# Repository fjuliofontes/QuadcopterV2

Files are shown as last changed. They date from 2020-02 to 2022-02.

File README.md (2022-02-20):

# Quadcopter V2
## This repository contains a work in progress of the second version of my previous quadcopter project.
## This version will support all modes of control.

### Main controller board hardware:
  - 1 x [ESP-01 for Wifi support](https://www.aliexpress.com/item/33018645469.html)
  - 1 x [HC-SR04 for landing support](https://www.aliexpress.com/item/32981718332.html)
  - 1 x [HC-05 for Bluetooth support](https://www.aliexpress.com/item/32953559442.html)
  - 2 x [HC-12 for RF communication](https://www.aliexpress.com/item/32971735328.html)
  - 1 x [MPU-6050 gyro/accelerometer for auto-level feature](https://www.aliexpress.com/item/32346328217.html)
  - 1 x [MS5611 Barometer for altitude hold function](https://www.aliexpress.com/item/4000436844936.html)
  - 1 x [SIM800L V2 for GSM & TCP communication](https://www.aliexpress.com/item/32467842817.html)
  - 1 x [U-blox M8 Engine GPS for heading lock and GPS hold function](https://www.dx.com/p/72-channel-u-blox-m8-engine-gps-module-for-fpv-multicopter-black-2069966.html)
  - 1 x [Texas-EK-TM4C123GXL for running the main software](http://www.ti.com/tool/EK-TM4C123GXL)
  
 ### Quadcopter housing hardware:
  - 1 x [450 size frame with integrated power distribution board](https://www.aliexpress.com/item/4000129400366.html)
  - 4 x [1000kV motor / 10x4.5 props / ESC combo](https://www.aliexpress.com/item/2035093137.html)
  - 1 x [3S / 2200mAh / 30C lipo](https://www.dx.com/p/11-1v-2200mah-30c-li-polymer-battery-pack-for-450-helicopter-dji-phantom-1-450-quadcopter-2048977.html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)
  - 1 x [Battery XT60 connector](https://www.aliexpress.com/item/33061763696.html)
  - 1 x [2S/3S lipo battery charger](https://www.aliexpress.com/item/4000106254839.html)
  
  #### [Version 1.0](https://github.com/fjuliofontes/Quadcopter)
  
  ##### TODO:
  - [x] Order the necessary hardware.
  - [x] Test and develop code for ordered hardware.
  - [x] Design a schematic and a board for the hardware.
  - [x] Develop a controller algorithm for the quadcopter.
  - [x] Update the android remote controller application.
  - [x] Testing all together. 
  
  ##### Media:
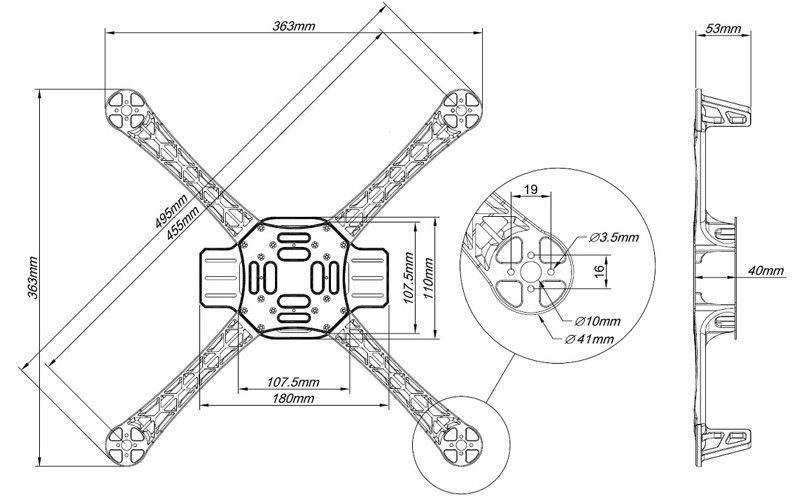
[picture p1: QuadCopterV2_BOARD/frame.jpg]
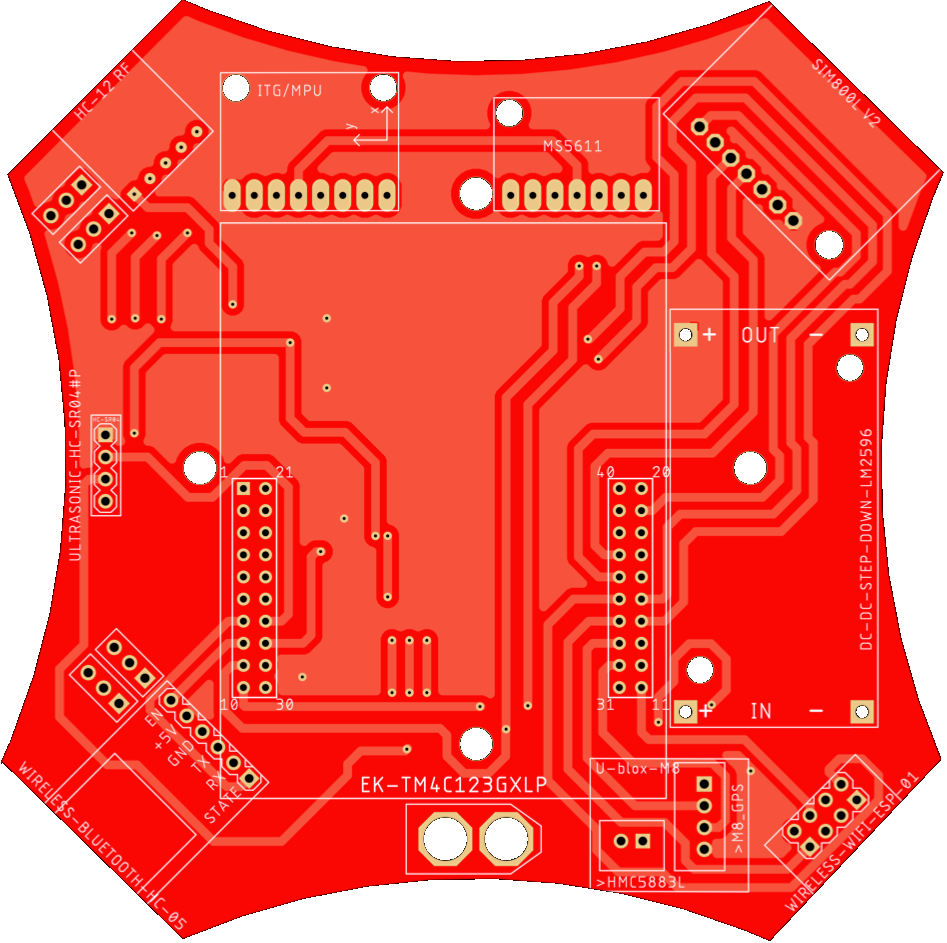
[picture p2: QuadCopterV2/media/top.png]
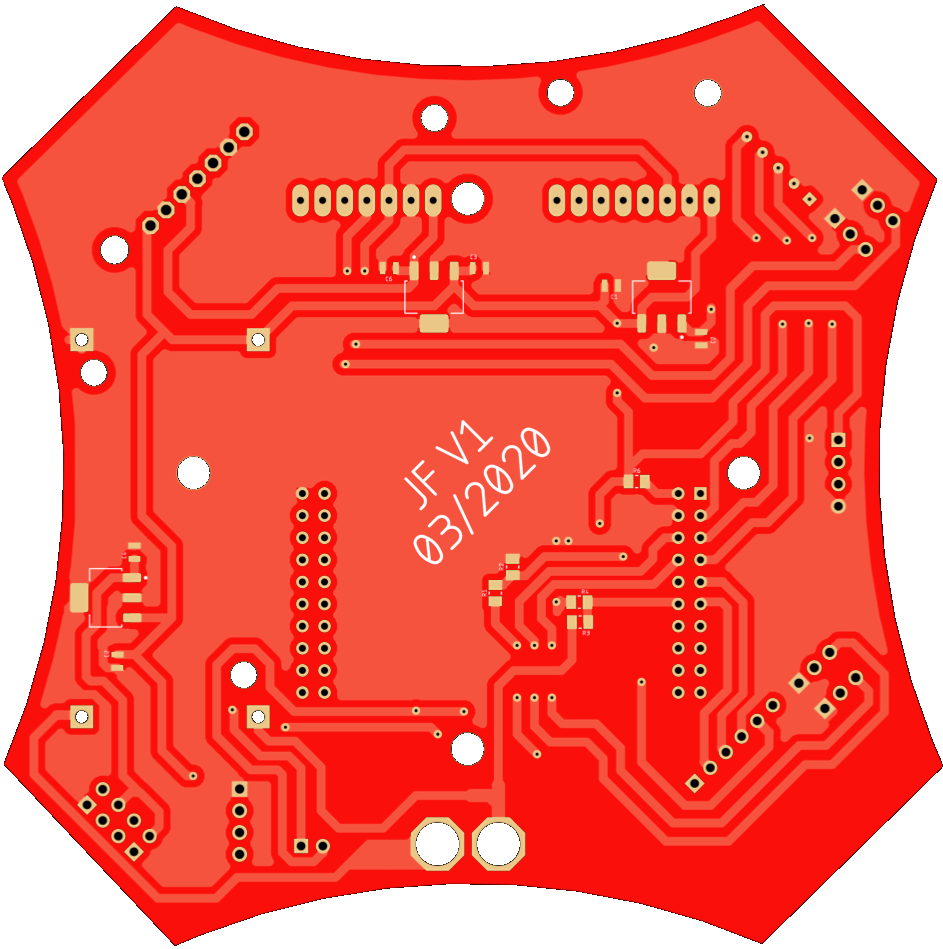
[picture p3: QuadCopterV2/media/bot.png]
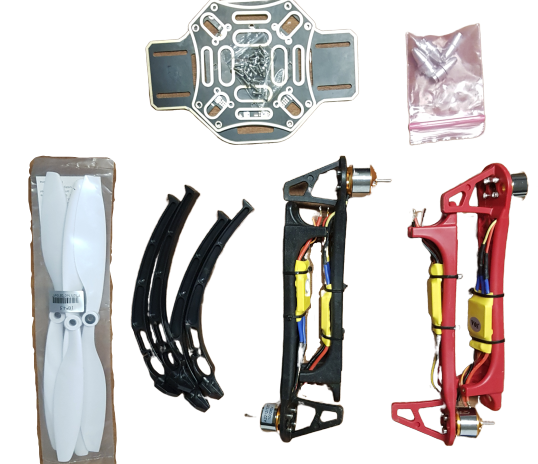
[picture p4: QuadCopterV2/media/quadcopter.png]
     
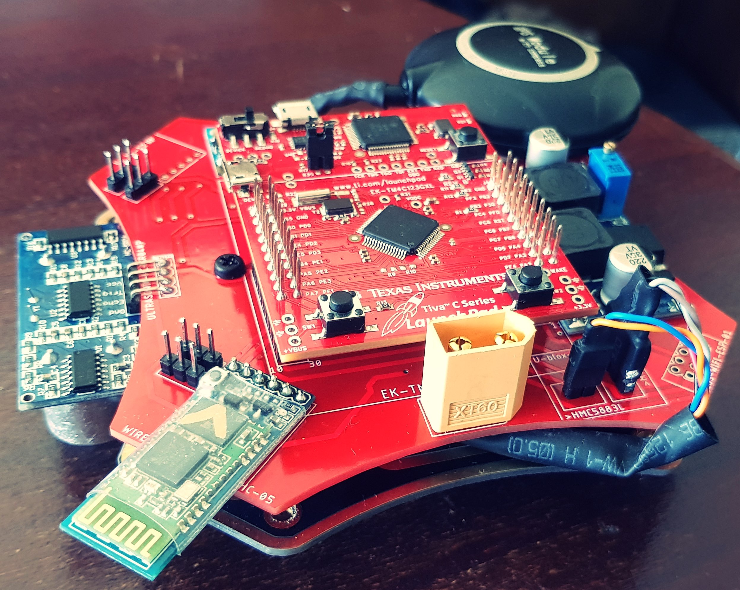
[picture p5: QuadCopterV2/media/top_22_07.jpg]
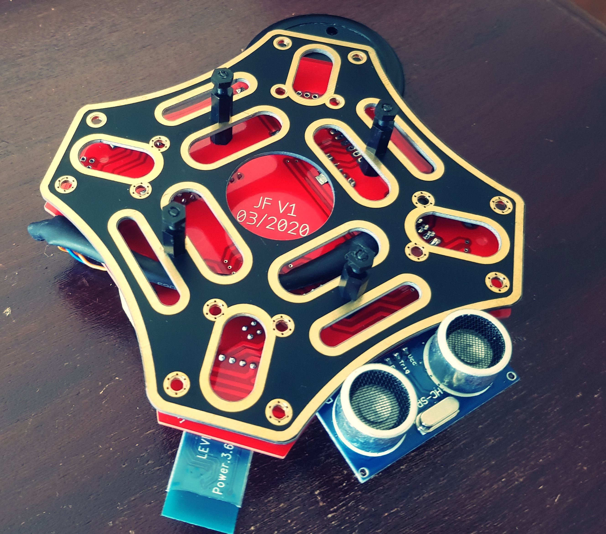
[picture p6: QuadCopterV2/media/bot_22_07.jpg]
   


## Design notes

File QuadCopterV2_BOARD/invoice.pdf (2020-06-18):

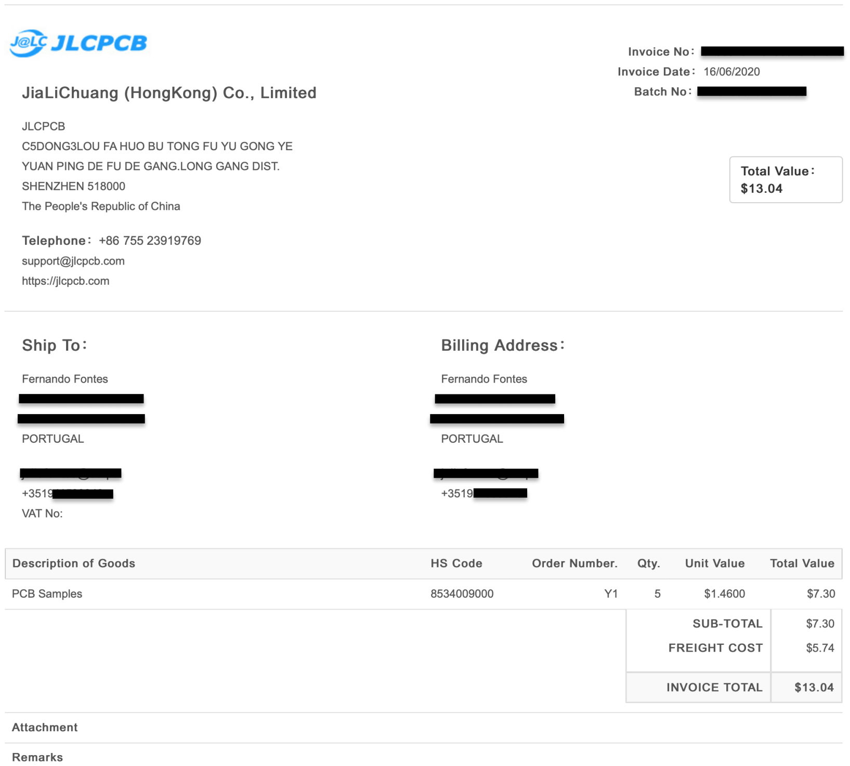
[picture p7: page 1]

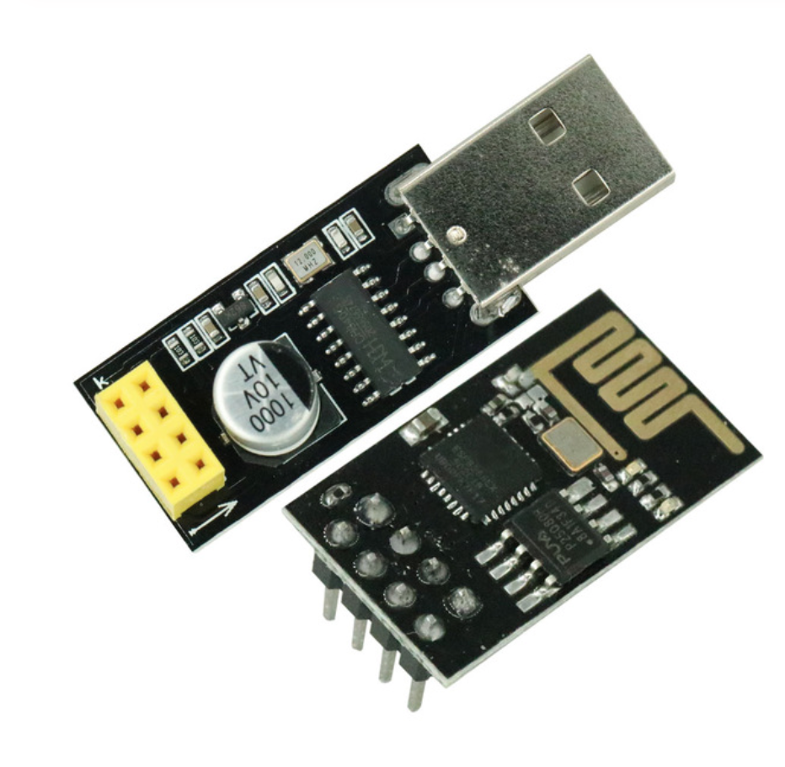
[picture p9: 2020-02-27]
ESP-01 (UART)/img/esp-01.png

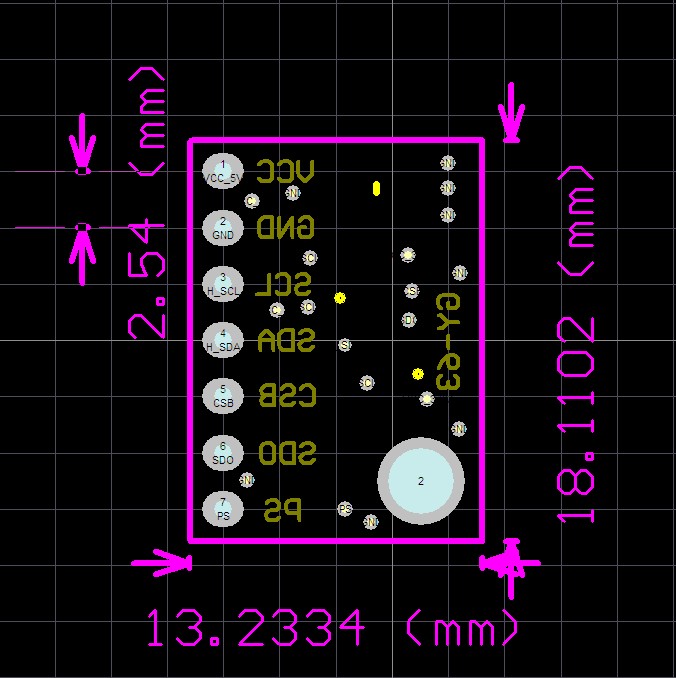
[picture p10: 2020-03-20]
MS5611 (I2C)/img/gy-63.jpg

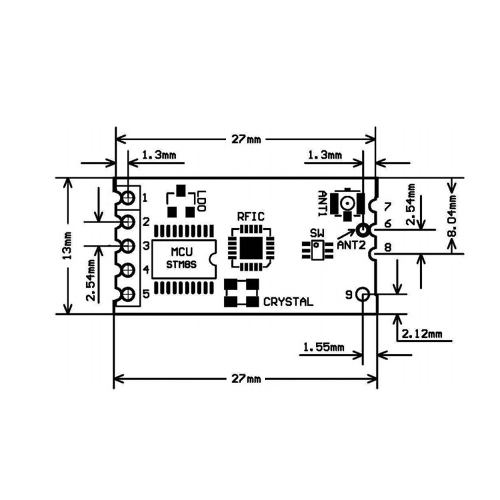
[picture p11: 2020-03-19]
HC-12 (UART)/img/hc-12-diagram.jpg

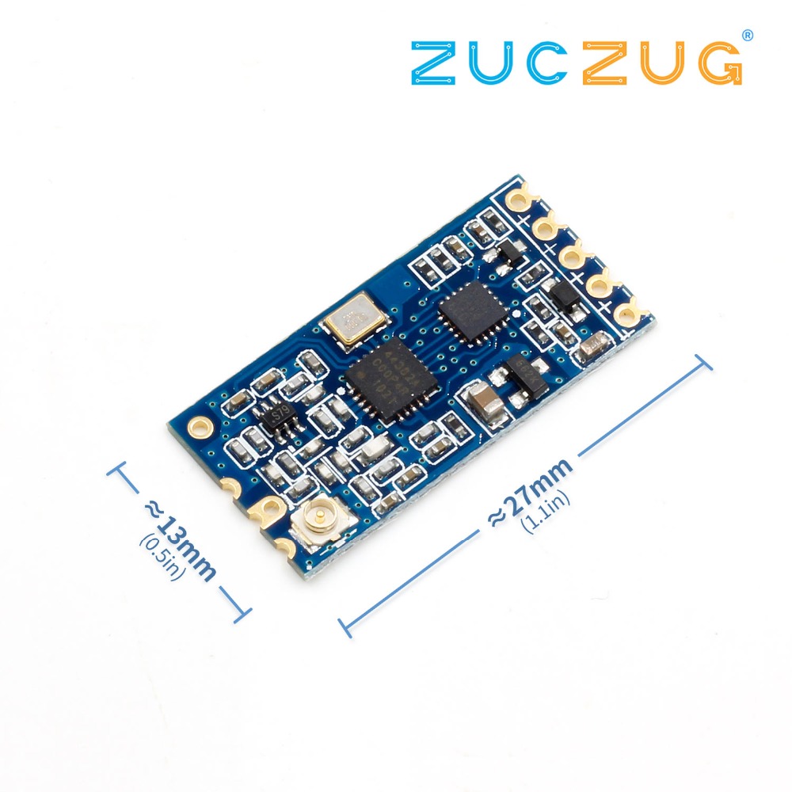
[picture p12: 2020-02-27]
HC-12 (UART)/img/HC-12_0.jpg

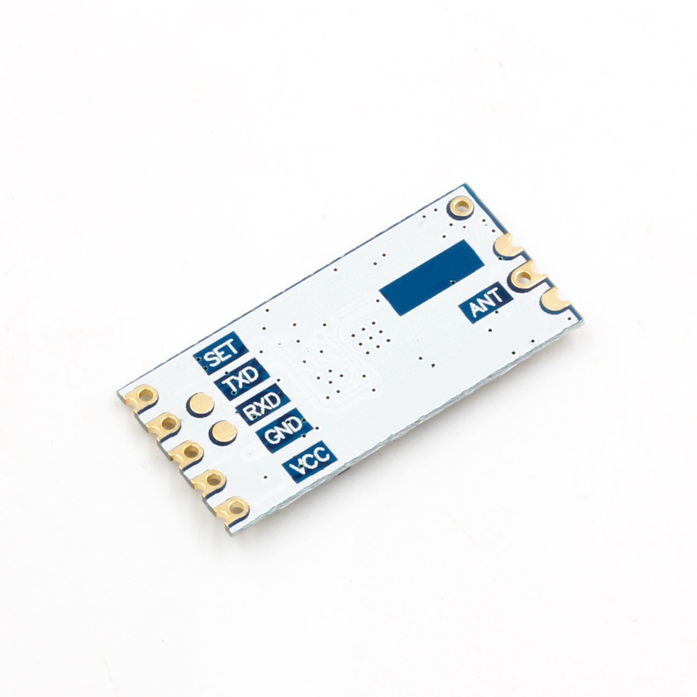
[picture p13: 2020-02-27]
HC-12 (UART)/img/HC-12_2.jpg

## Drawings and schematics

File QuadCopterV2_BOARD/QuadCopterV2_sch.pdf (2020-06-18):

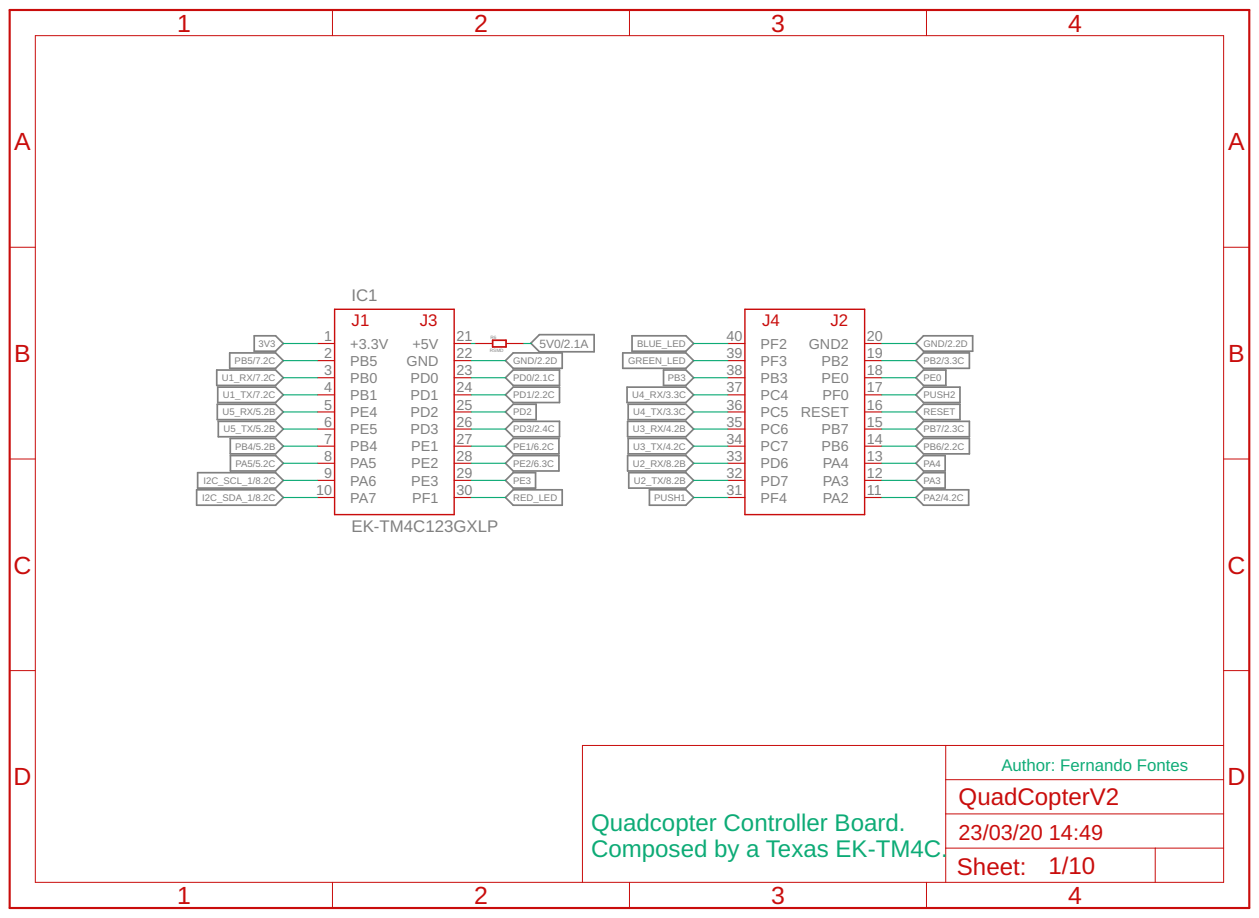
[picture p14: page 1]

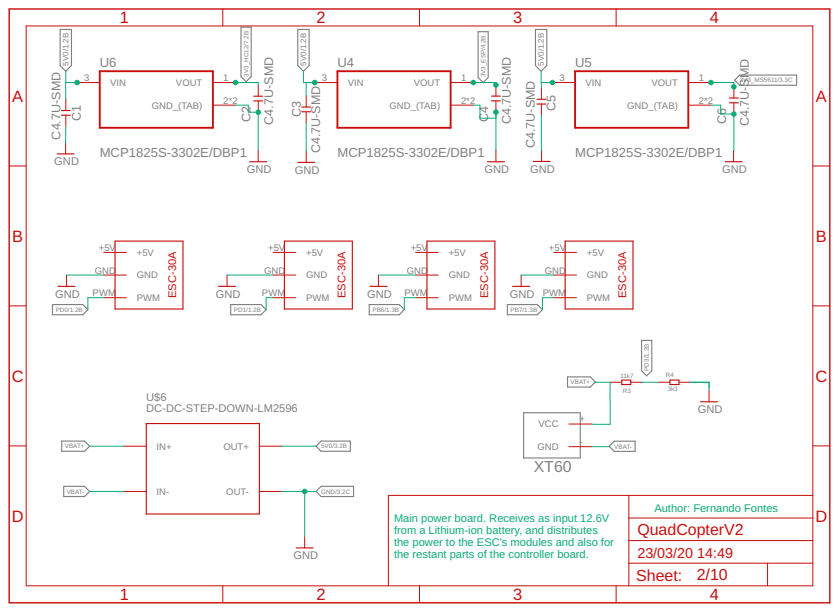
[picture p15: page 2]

DC-DC-STEP-DOWN-LM2596

Main power board. Receives as input 12.6V
from a Lithium-ion battery, and distributes
the power to the ESC's modules and also for

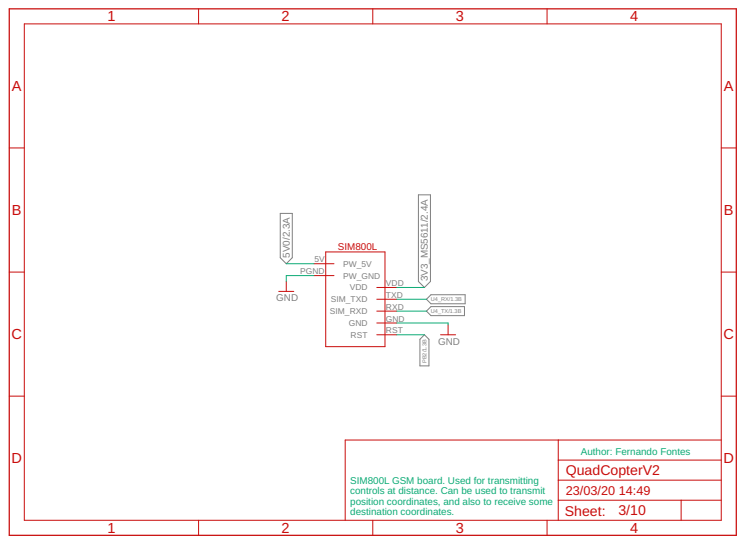
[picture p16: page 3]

Author: Fernando Fontes SIM800L GSM board. Used for transmitting

controls at distance. Can be used to transmit
position coordinates, and also to receive some
destination coordinates.

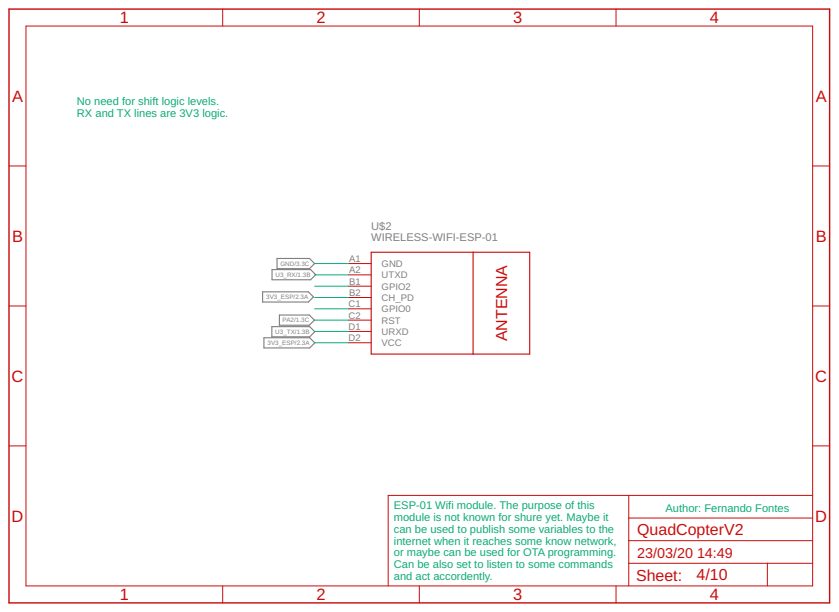
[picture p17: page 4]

No need for shift logic levels. RX and TX lines are 3V3 logic.

WIRELESS-WIFI-ESP-01 GND

-01 Wifi module. The purpose of this module is not known for shure yet. Maybe it can be used to publish some variables to the

internet when it reaches some know network, or maybe can be used for OTA programming. Can be also set to listen to some commands and act accordently.

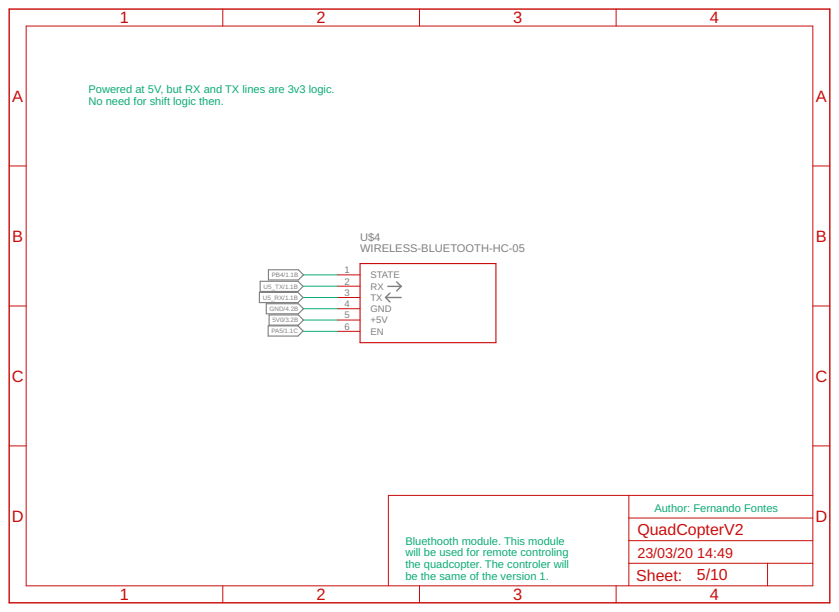
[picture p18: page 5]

Powered at 5V, but RX and TX lines are 3v3 logic. No need for shift logic then.

WIRELESS-BLUETOOTH-HC-05 STATE

the quadcopter. The controler will be the same of the version 1. | Author: Fernando Fontes Bluethooth module. This module will be used for remote controling

Sheet: 5/10

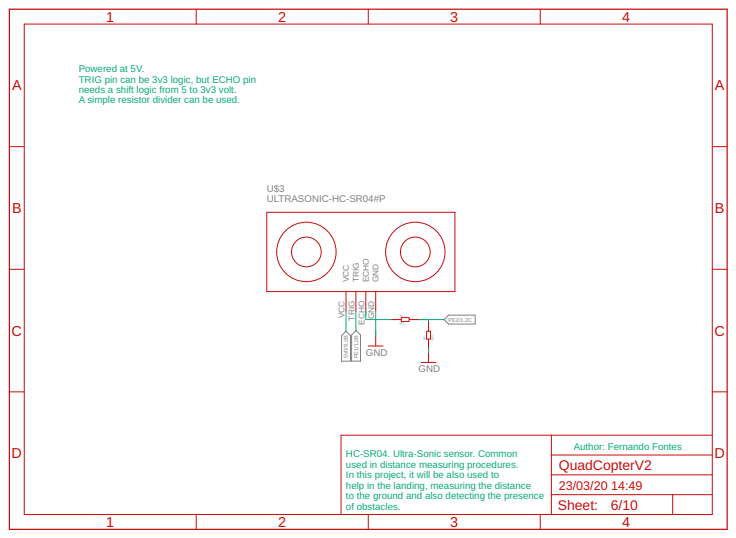
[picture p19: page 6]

Powered at 5V. TRIG pin can be 3v3 logic, but ECHO pin
needs a shift logic from 5 to 3v3 volt. A simple resistor divider can be used.

used in distance measuring procedures. In this project, it will be also used to help in the landing, measuring the distance to the ground and also detecting the presence of obstacles. | Author: Fernando Fontes HC-SR04. Ultra-Sonic sensor. Common

Sheet: 6/10

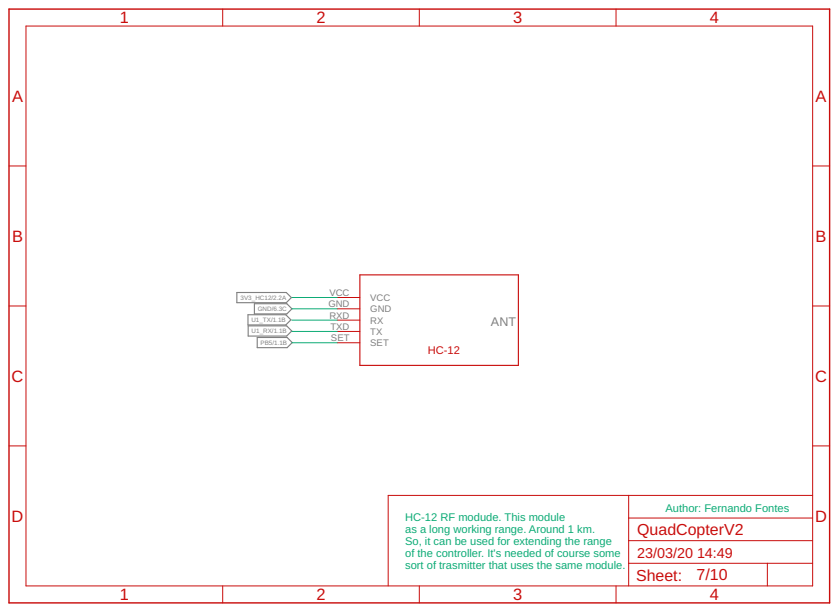
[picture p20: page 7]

as a long working range. Around 1 km. So, it can be used for extending the range of the controller. It's needed of course some sort of trasmitter that uses the same module. | Author: Fernando Fontes HC-12 RF modude. This module

Sheet: 7/10

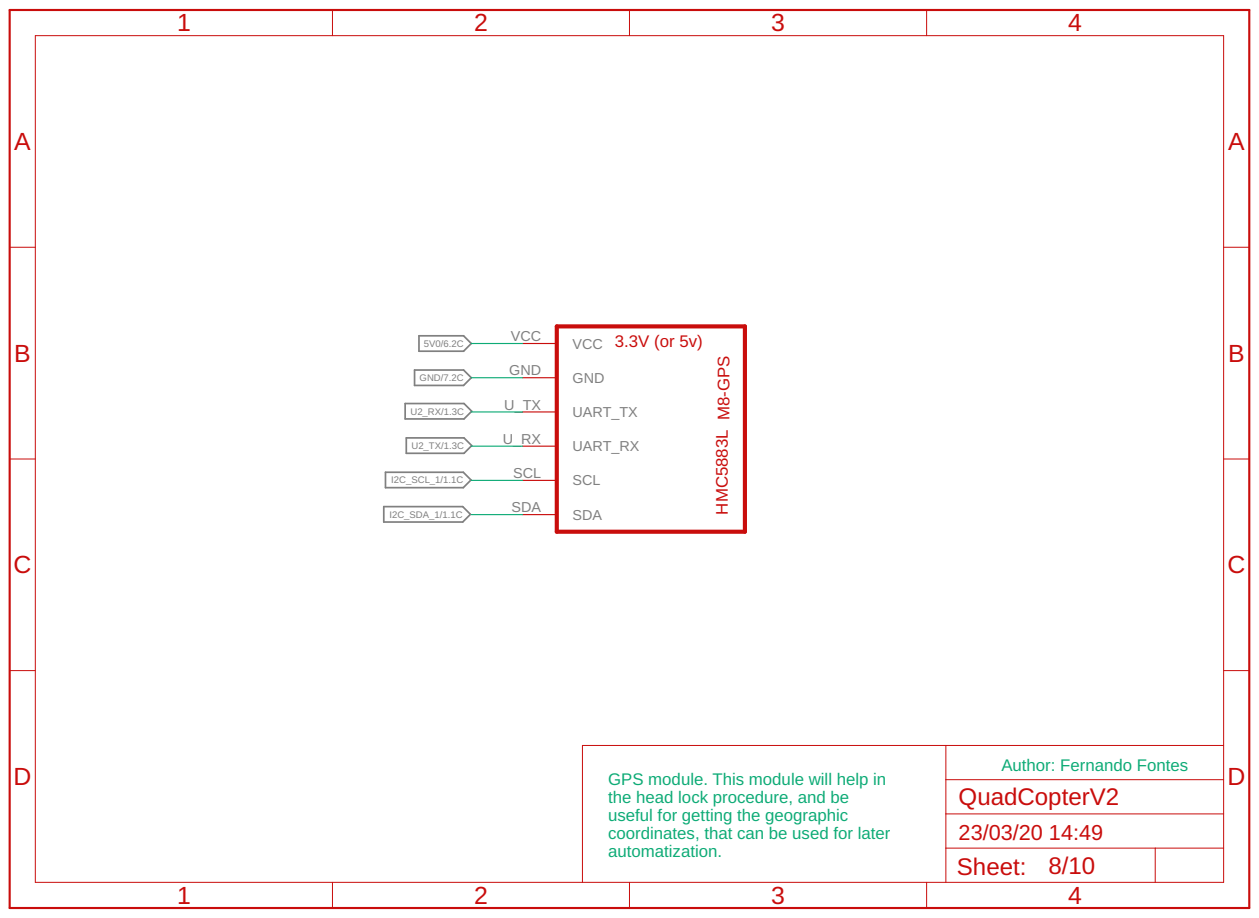
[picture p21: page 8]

Author: Fernando Fontes GPS module. This module will help in
the head lock procedure, and be
useful for getting the geographic
coordinates, that can be used for later automatization.

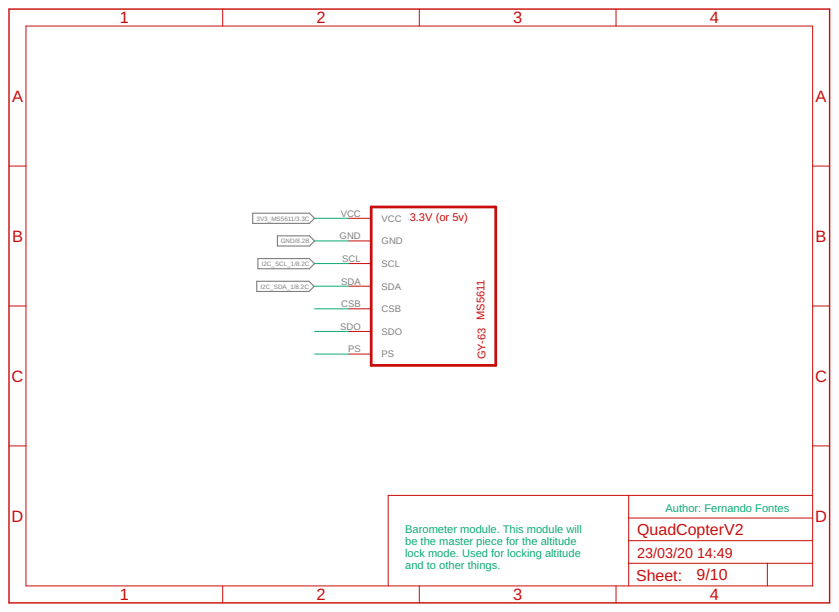
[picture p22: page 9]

be the master piece for the altitude lock mode. Used for locking altitude and to other things. | Author: Fernando Fontes Barometer module. This module will

Sheet: 9/10

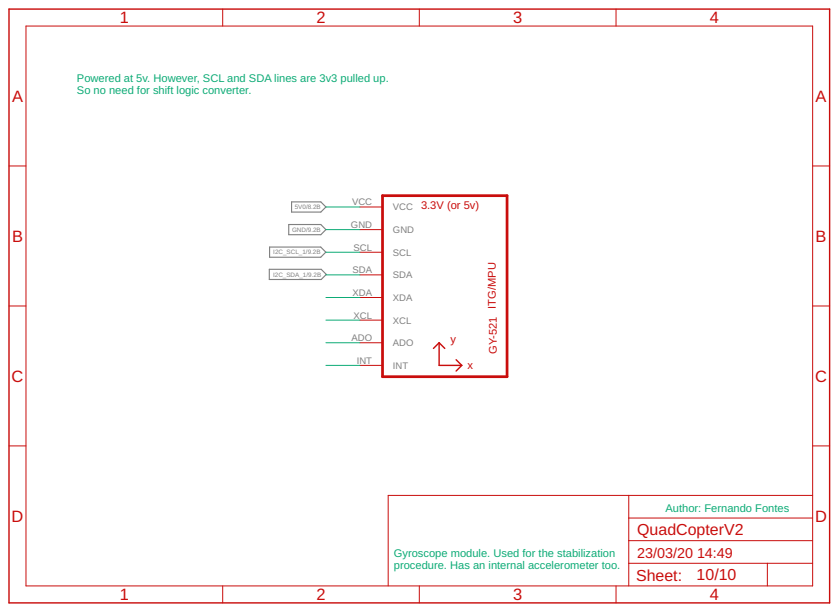
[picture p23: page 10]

Powered at 5v. However, SCL and SDA lines are 3v3 pulled up. So no need for shift logic converter.

Author: Fernando Fontes Gyroscope module. Used for the stabilization

procedure. Has an internal accelerometer too.

Sheet: 10/10

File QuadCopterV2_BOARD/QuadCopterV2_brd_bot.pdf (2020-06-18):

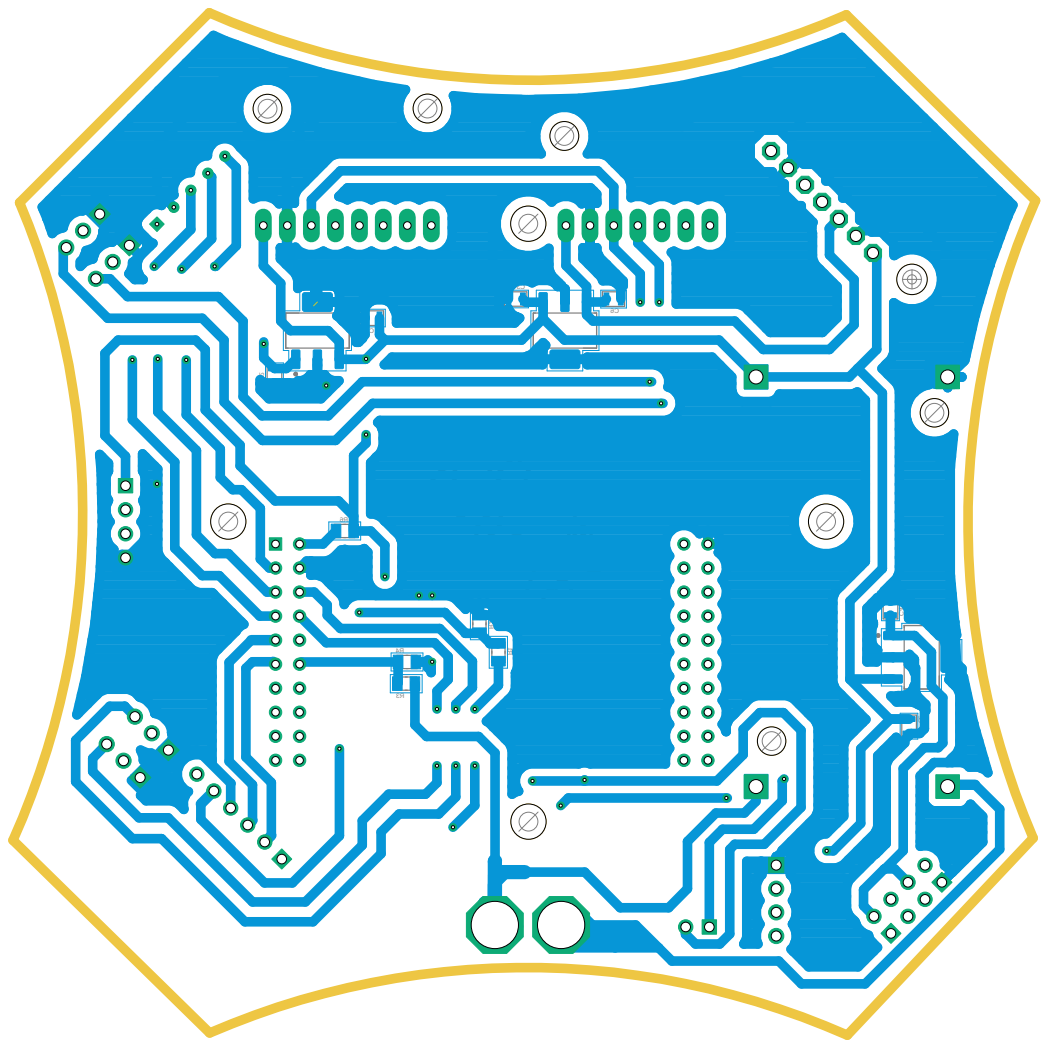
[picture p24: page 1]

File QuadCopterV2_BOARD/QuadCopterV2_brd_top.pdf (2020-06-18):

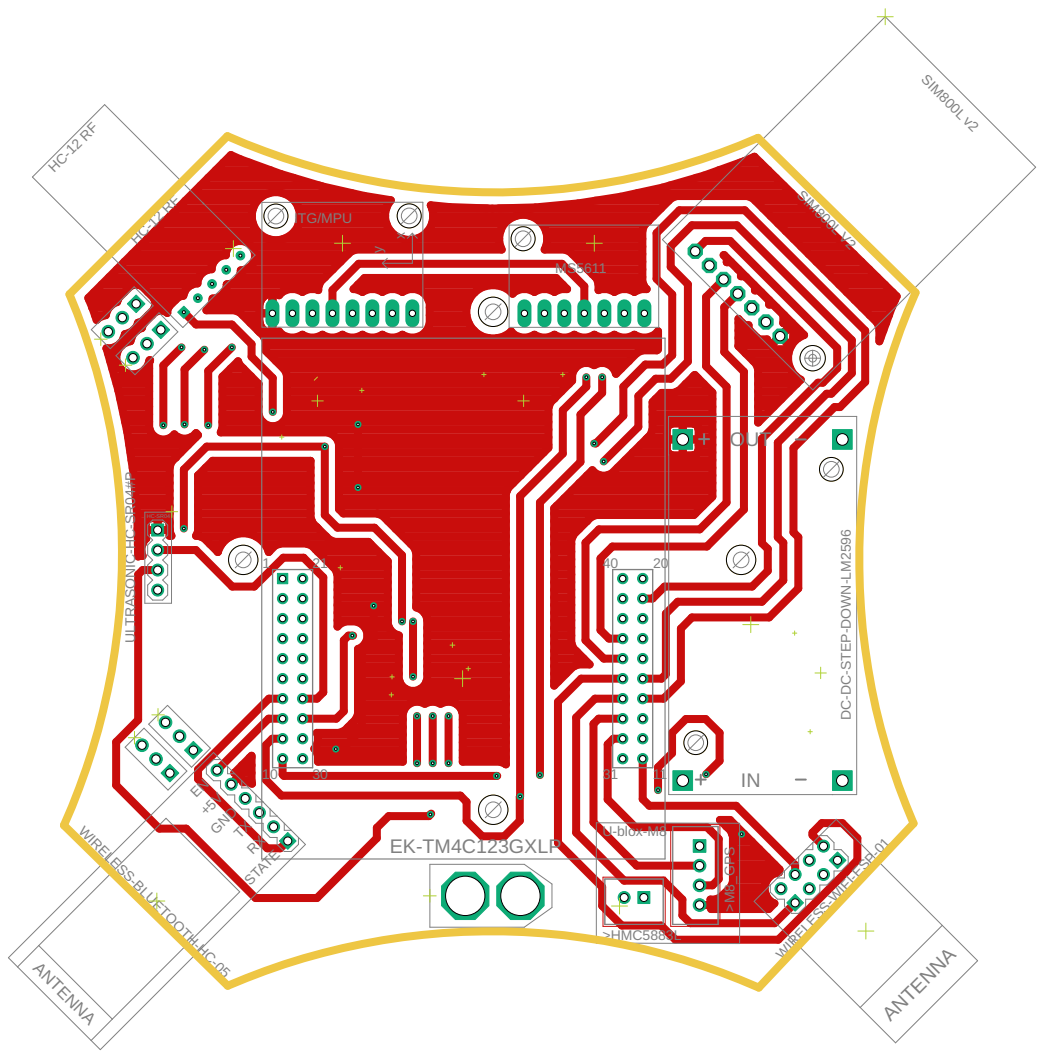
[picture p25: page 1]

DC-DC-STEP-DOWN-LM2596

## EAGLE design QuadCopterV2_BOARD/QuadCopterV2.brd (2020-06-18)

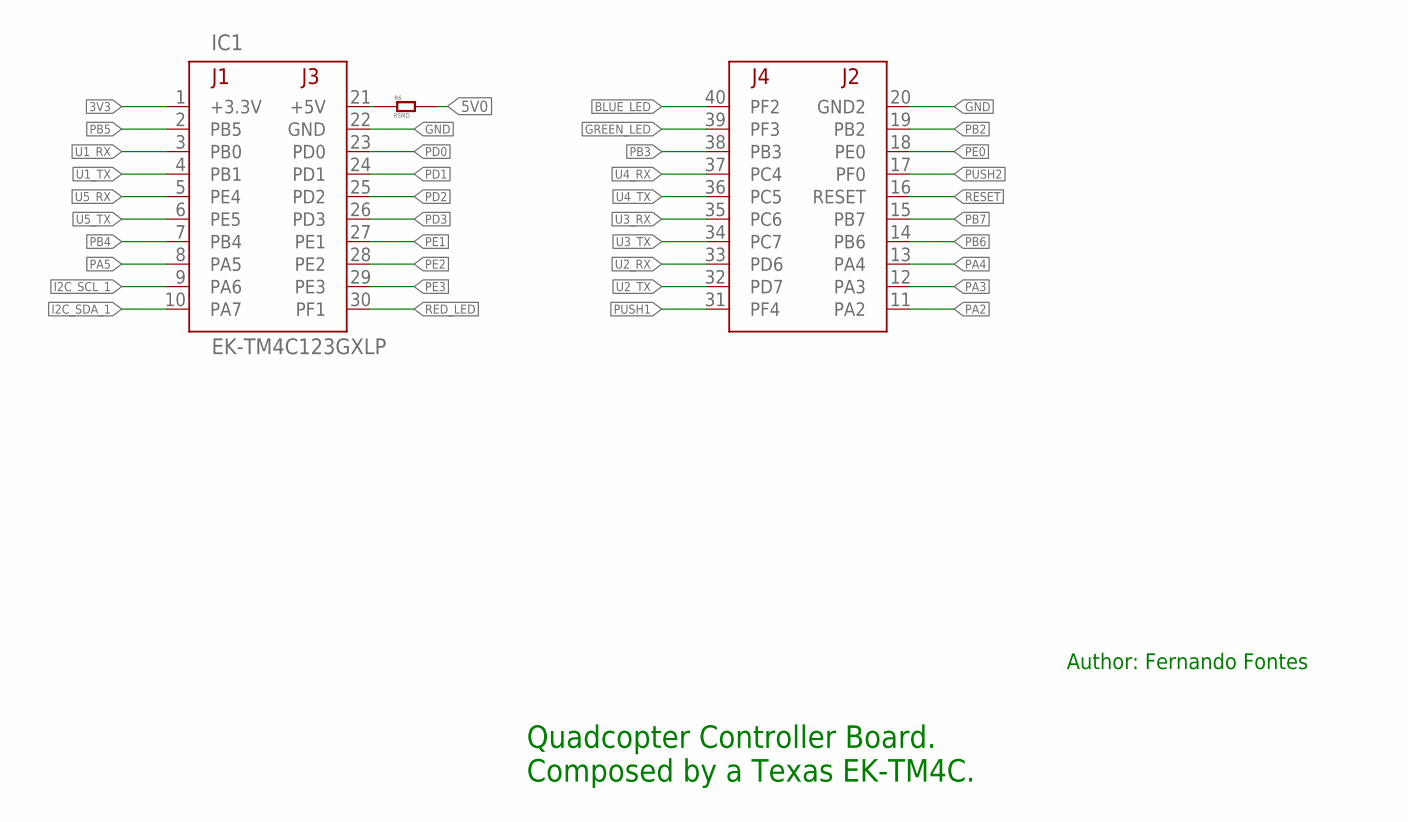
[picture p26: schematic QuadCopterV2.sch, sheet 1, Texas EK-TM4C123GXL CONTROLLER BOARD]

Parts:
IC1: EK-TM4C123GXLP; TM4C123LAUNCHPAD
R6: RSMD

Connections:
3V3: IC1.1 (+3.3V)
5V0: R6.2; also elsewhere on the board
BLUE_LED: IC1.40 (PF2)
GND: IC1.20 (GND2), IC1.22 (GND); also elsewhere on the board
GREEN_LED: IC1.39 (PF3)
I2C_SCL_1: IC1.9 (PA6); also elsewhere on the board
I2C_SDA_1: IC1.10 (PA7); also elsewhere on the board
unnamed: IC1.21 (+5V), R6.1
PA2: IC1.11 (PA2); also elsewhere on the board
PA3: IC1.12 (PA3)
PA4: IC1.13 (PA4)
PA5: IC1.8 (PA5); also elsewhere on the board
PB2: IC1.19 (PB2); also elsewhere on the board
PB3: IC1.38 (PB3)
PB4: IC1.7 (PB4); also elsewhere on the board
PB5: IC1.2 (PB5); also elsewhere on the board
PB6: IC1.14 (PB6); also elsewhere on the board
PB7: IC1.15 (PB7); also elsewhere on the board
PD0: IC1.23 (PD0); also elsewhere on the board
PD1: IC1.24 (PD1); also elsewhere on the board
PD2: IC1.25 (PD2)
PD3: IC1.26 (PD3); also elsewhere on the board
PE0: IC1.18 (PE0)
PE1: IC1.27 (PE1); also elsewhere on the board
PE2: IC1.28 (PE2); also elsewhere on the board
PE3: IC1.29 (PE3)
PUSH1: IC1.31 (PF4)
PUSH2: IC1.17 (PF0)
RED_LED: IC1.30 (PF1)
RESET: IC1.16 (RESET)
U1_RX: IC1.3 (PB0); also elsewhere on the board
U1_TX: IC1.4 (PB1); also elsewhere on the board
U2_RX: IC1.33 (PD6); also elsewhere on the board
U2_TX: IC1.32 (PD7); also elsewhere on the board
U3_RX: IC1.35 (PC6); also elsewhere on the board
U3_TX: IC1.34 (PC7); also elsewhere on the board
U4_RX: IC1.37 (PC4); also elsewhere on the board
U4_TX: IC1.36 (PC5); also elsewhere on the board
U5_RX: IC1.5 (PE4); also elsewhere on the board
U5_TX: IC1.6 (PE5); also elsewhere on the board

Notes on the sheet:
Quadcopter Controller Board. Composed by a Texas EK-TM4C.
Author: Fernando Fontes

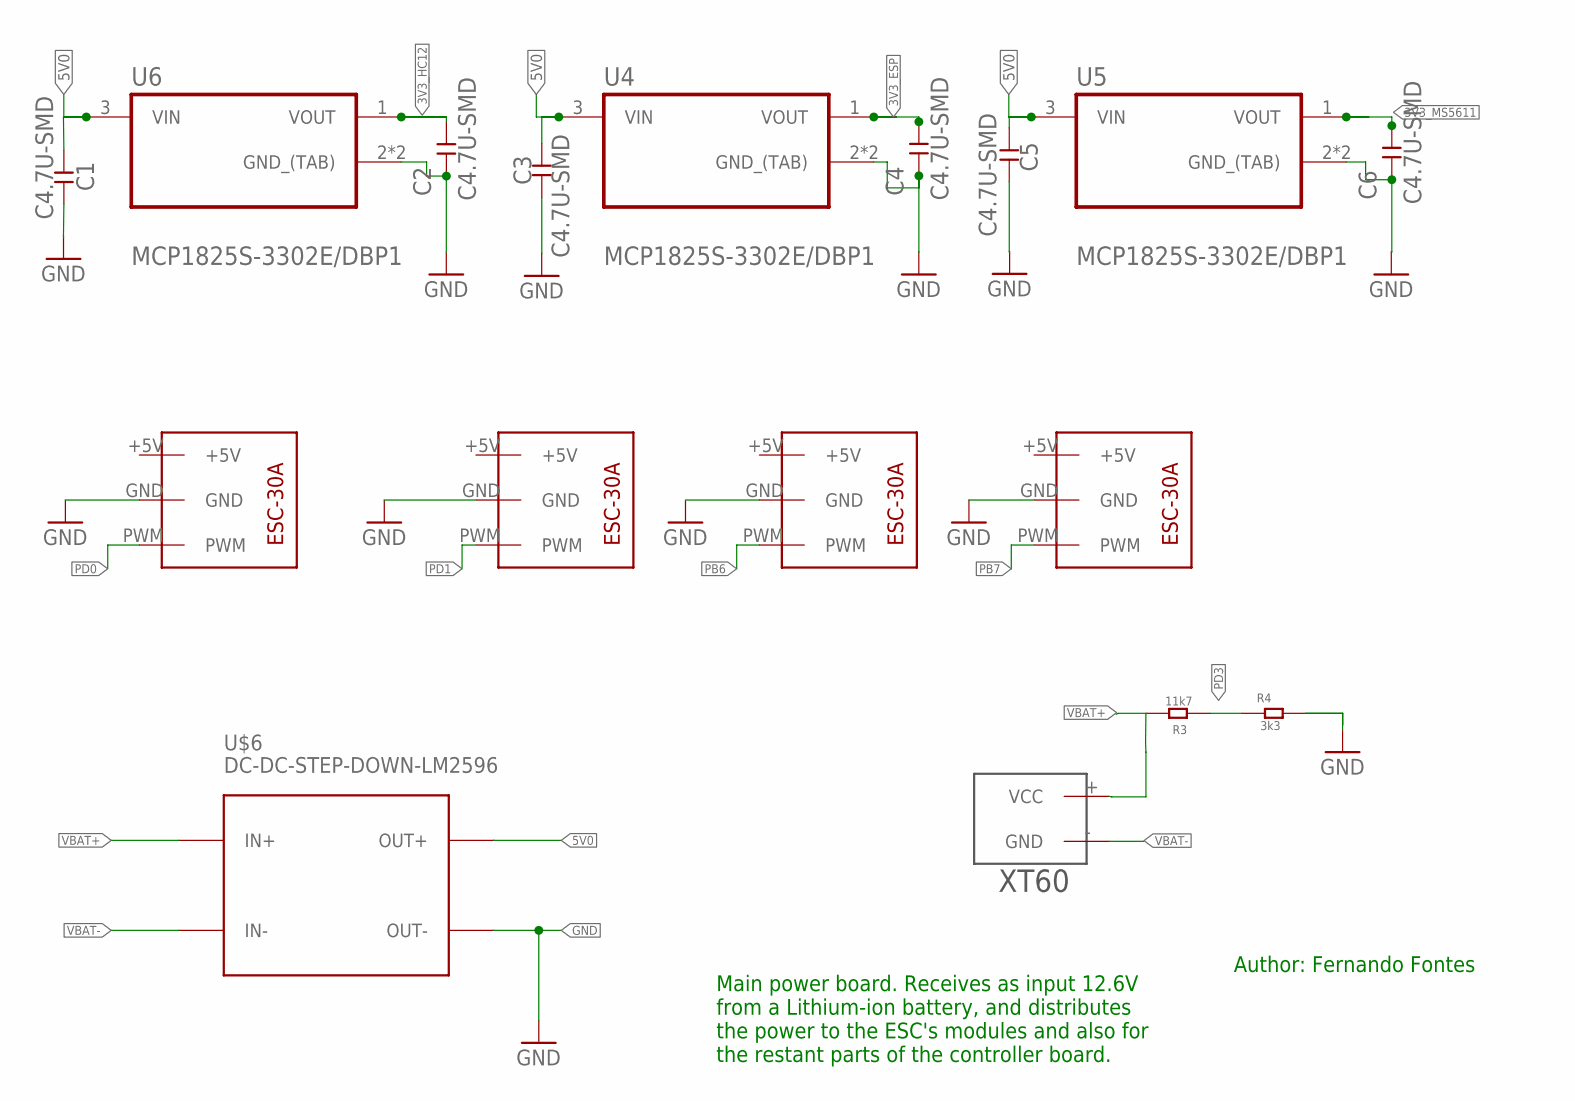
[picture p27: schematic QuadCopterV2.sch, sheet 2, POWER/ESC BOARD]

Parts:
C1, C2, C3, C4, C5, C6: C4.7U-SMD
R3: 11k7; RSMD
R4: 3k3; RSMD
U4, U5, U6: MCP1825S-3302E/DBP1; SOT230P700X180-4N#P1
U7, U8, U9, U10: ESC-30AMS5611; ESC-30A
U$6: DC-DC-STEP-DOWN-LM2596
U$7: XT60

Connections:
3V3_ESP: C4.2, U4.1 (VOUT); also elsewhere on the board
3V3_HC12: C2.2, U6.1 (VOUT); also elsewhere on the board
3V3_MS5611: C6.2, U5.1 (VOUT); also elsewhere on the board
5V0: C1.1, C3.2, C5.1, U4.3 (VIN), U5.3 (VIN), U6.3 (VIN), U$6.OUT+; also elsewhere on the board
GND: C1.2, C2.1, C3.1, C4.1, C5.2, C6.1, R4.2, U4.2 (GND_(TAB)), U4.4 (GND_(TAB)), U5.2 (GND_(TAB)), U5.4 (GND_(TAB)), U6.2 (GND_(TAB)), U6.4 (GND_(TAB)), U7.GND, U8.GND, U9.GND, U10.GND, U$6.OUT-; also elsewhere on the board
PB6: U9.PWM; also elsewhere on the board
PB7: U10.PWM; also elsewhere on the board
PD0: U7.PWM; also elsewhere on the board
PD1: U8.PWM; also elsewhere on the board
PD3: R3.1, R4.1; also elsewhere on the board
VBAT+: R3.2, U$6.IN+, U$7.+ (VCC)
VBAT-: U$6.IN-, U$7.- (GND)

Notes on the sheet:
Main power board. Receives as input 12.6V from a Lithium-ion battery, and distributes the power to the ESC's modules and also for the restant parts of the controller board.
Author: Fernando Fontes

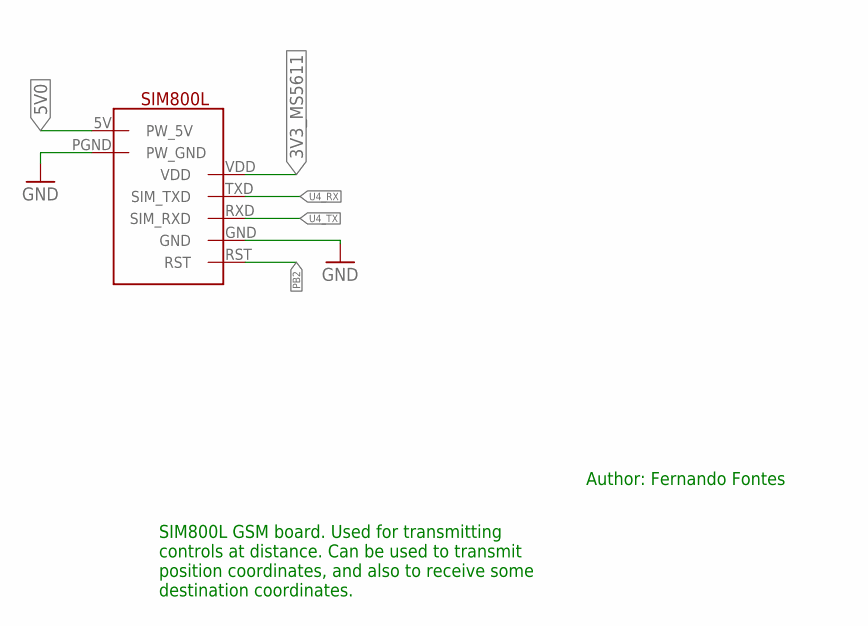
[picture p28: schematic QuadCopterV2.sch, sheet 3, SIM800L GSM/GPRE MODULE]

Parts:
U$1: SIM800L; SIP

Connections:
3V3_MS5611: U$1.VDD; also elsewhere on the board
5V0: U$1.5V (PW_5V); also elsewhere on the board
GND: U$1.GND, U$1.PGND (PW_GND); also elsewhere on the board
PB2: U$1.RST; also elsewhere on the board
U4_RX: U$1.TXD (SIM_TXD); also elsewhere on the board
U4_TX: U$1.RXD (SIM_RXD); also elsewhere on the board

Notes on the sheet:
Author: Fernando Fontes
SIM800L GSM board. Used for transmitting controls at distance. Can be used to transmit position coordinates, and also to receive some destination coordinates.

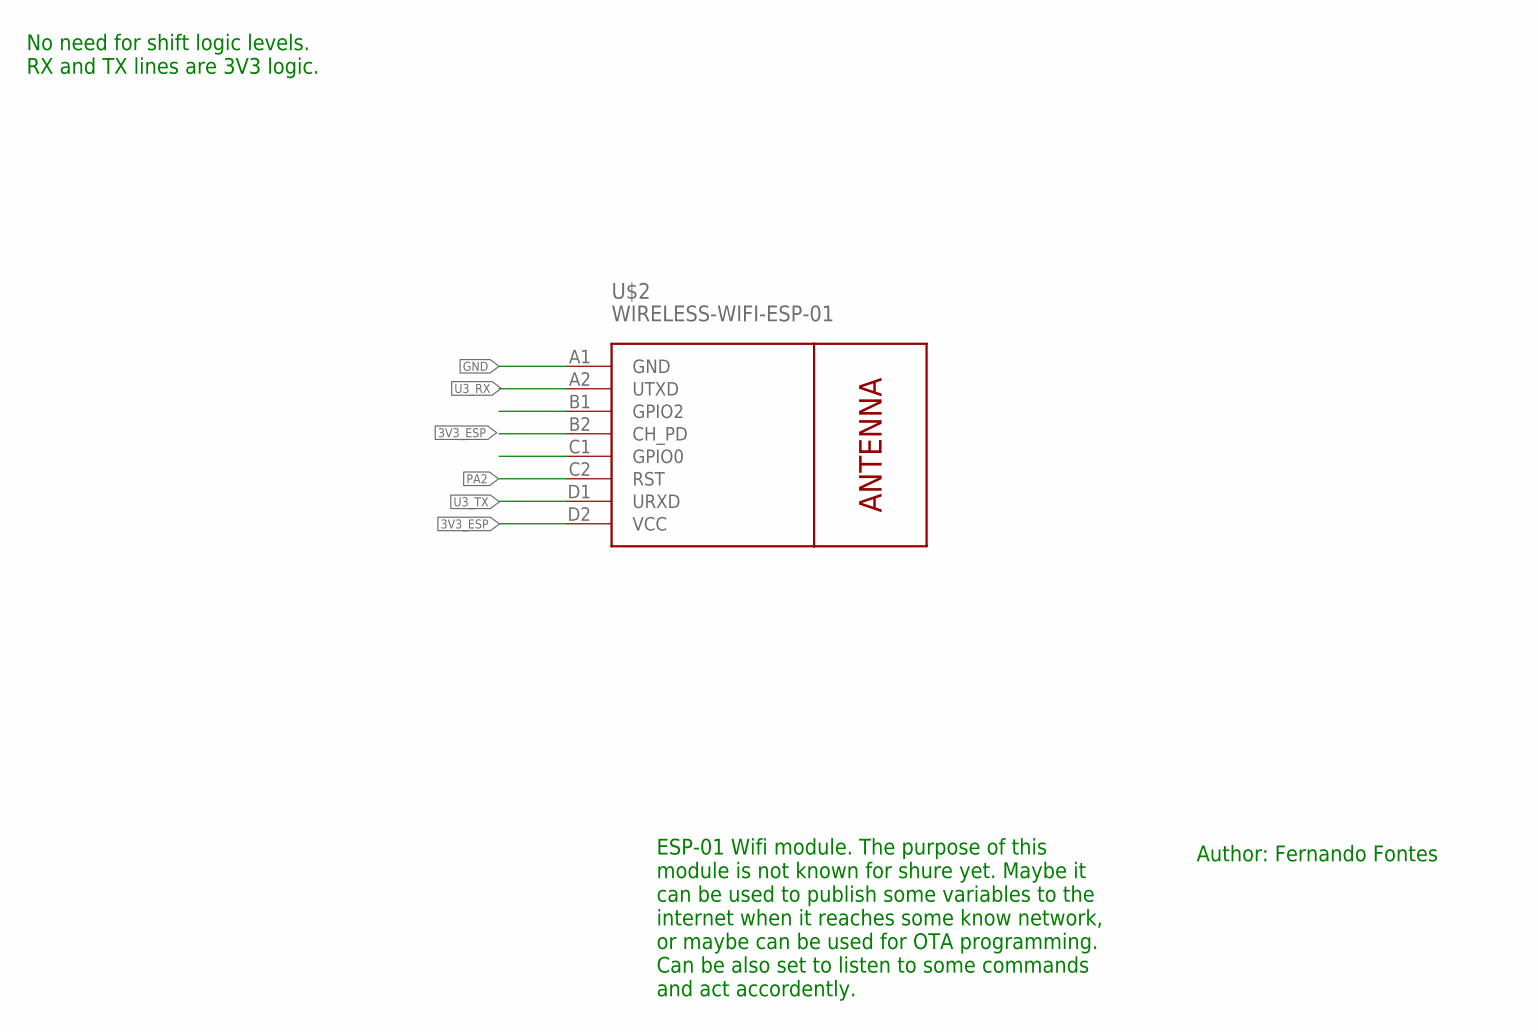
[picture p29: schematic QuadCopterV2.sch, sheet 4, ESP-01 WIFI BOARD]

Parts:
U$2: WIRELESS-WIFI-ESP-01

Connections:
3V3_ESP: U$2.B2 (CH_PD), U$2.D2 (VCC); also elsewhere on the board
GND: U$2.A1 (GND); also elsewhere on the board
PA2: U$2.C2 (RST); also elsewhere on the board
U3_RX: U$2.A2 (UTXD); also elsewhere on the board
U3_TX: U$2.D1 (URXD); also elsewhere on the board

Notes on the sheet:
No need for shift logic levels. RX and TX lines are 3V3 logic.
Author: Fernando Fontes
ESP-01 Wifi module. The purpose of this module is not known for shure yet. Maybe it can be used to publish some variables to the internet when it reaches some know network, or maybe can be used for OTA programming. Can be also set to listen to some commands and act accordently.

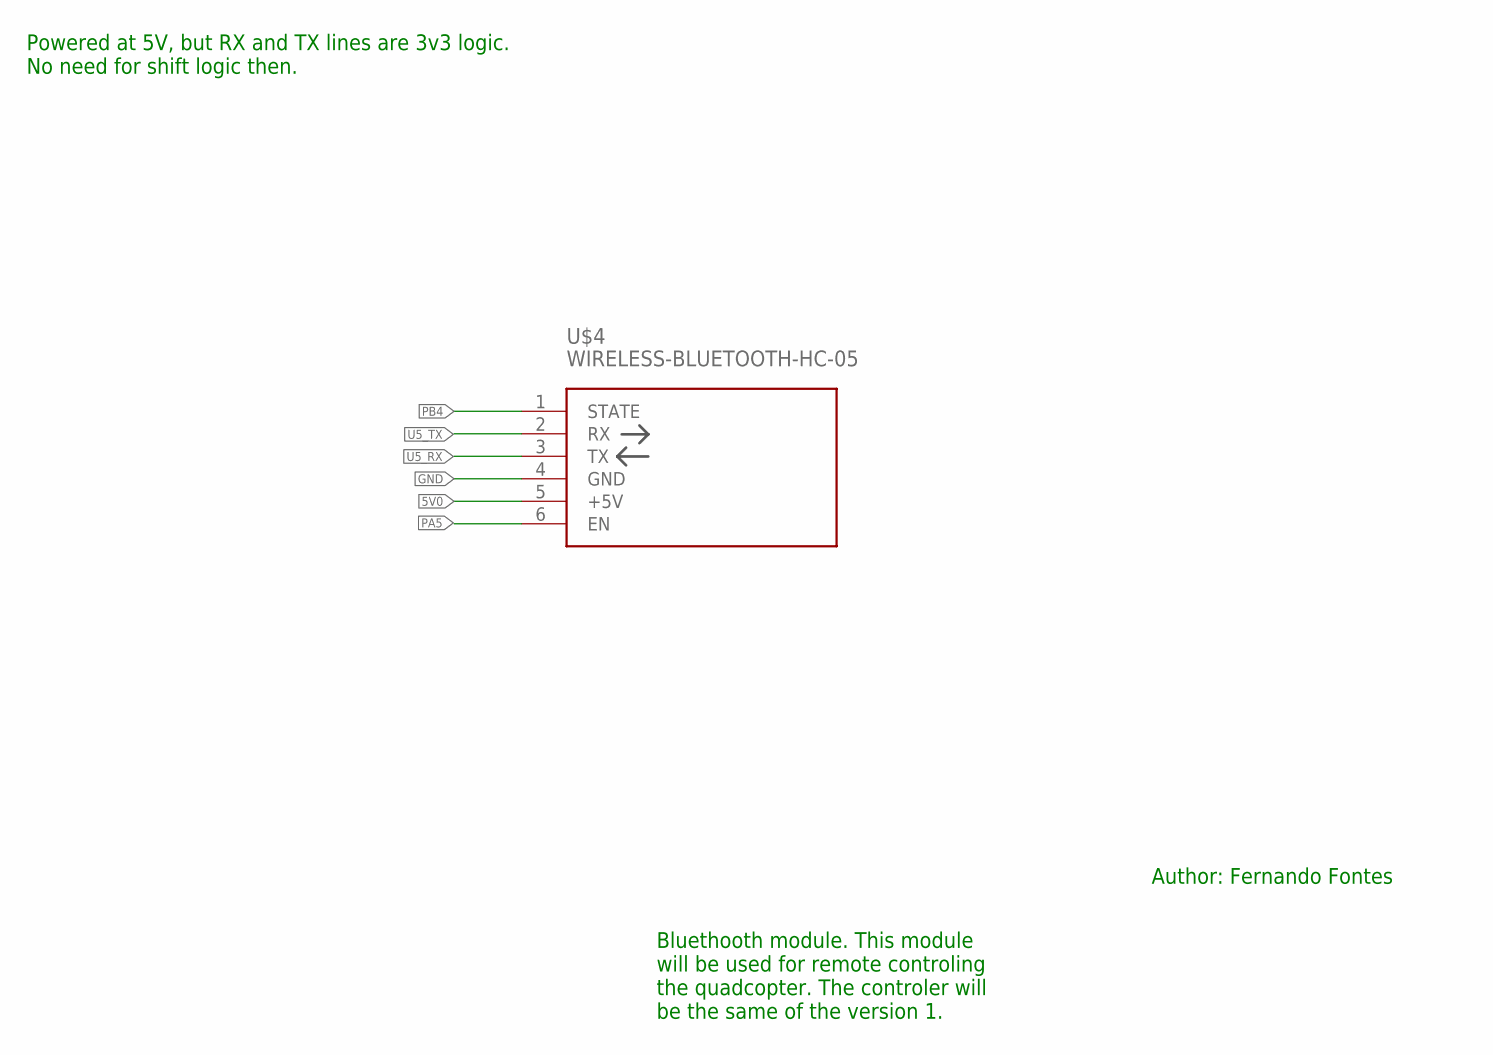
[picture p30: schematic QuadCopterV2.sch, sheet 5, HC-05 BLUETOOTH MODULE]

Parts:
U$4: WIRELESS-BLUETOOTH-HC-05

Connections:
5V0: U$4.5 (+5V); also elsewhere on the board
GND: U$4.4 (GND); also elsewhere on the board
PA5: U$4.6 (EN); also elsewhere on the board
PB4: U$4.1 (STATE); also elsewhere on the board
U5_RX: U$4.3 (TX); also elsewhere on the board
U5_TX: U$4.2 (RX); also elsewhere on the board

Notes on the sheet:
Powered at 5V, but RX and TX lines are 3v3 logic. No need for shift logic then.
Author: Fernando Fontes
Bluethooth module. This module will be used for remote controling the quadcopter. The controler will be the same of the version 1.

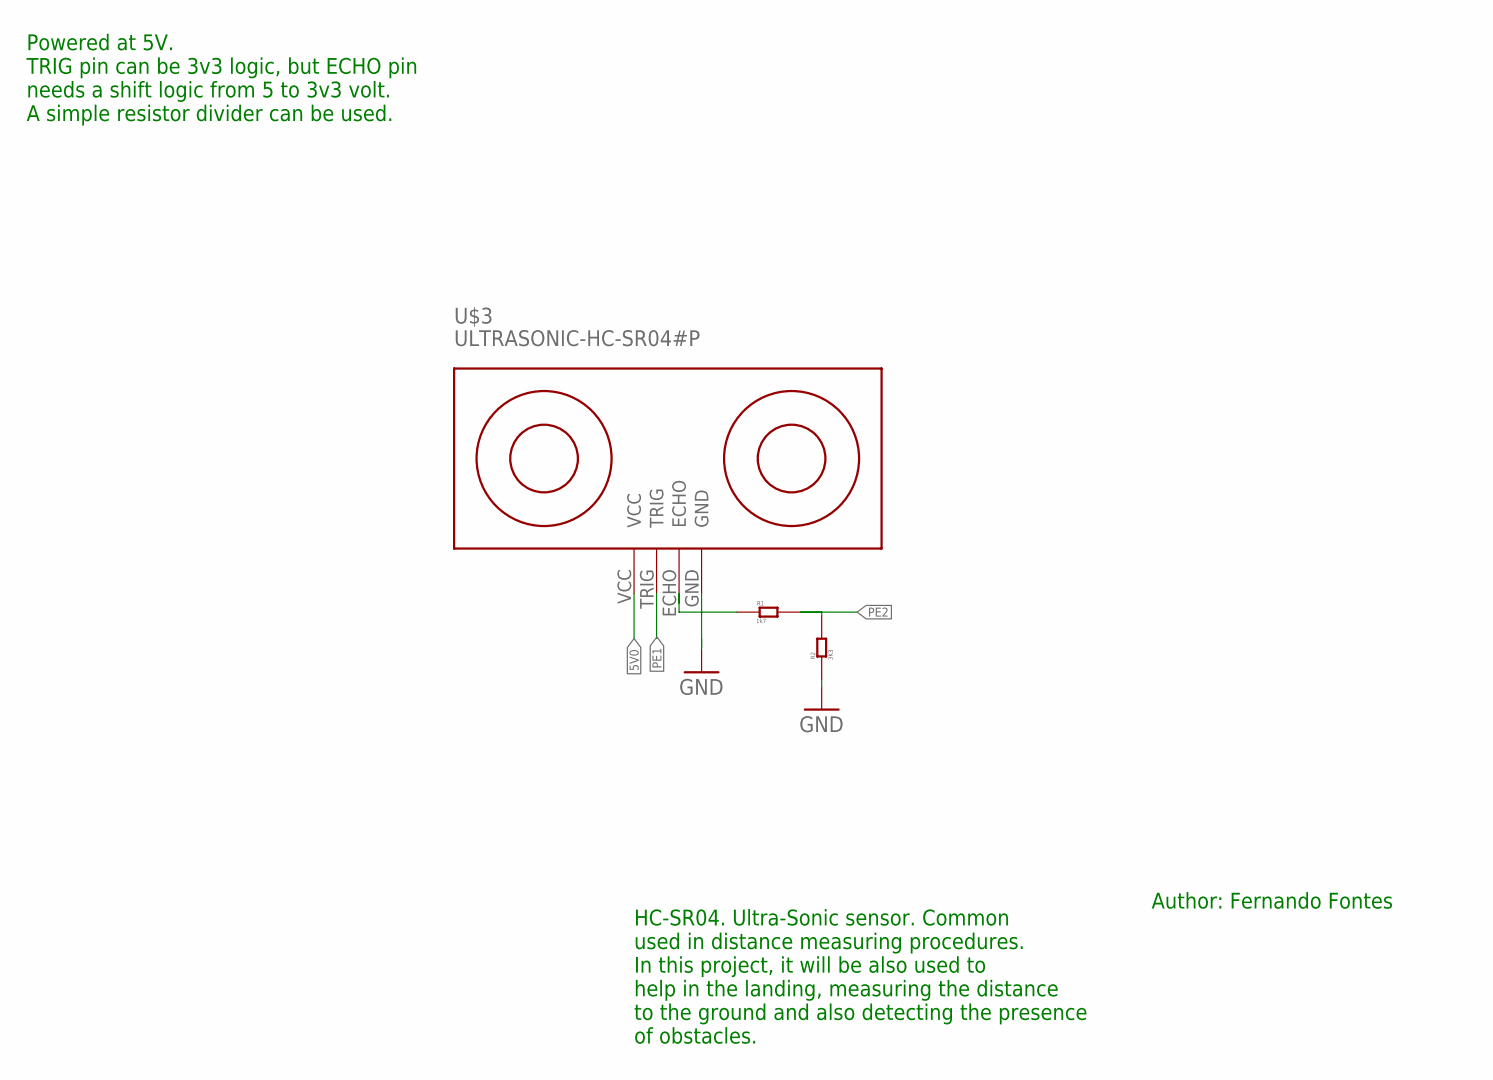
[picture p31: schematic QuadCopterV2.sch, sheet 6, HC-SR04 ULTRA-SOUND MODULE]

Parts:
R1: 1k7; RSMD
R2: 3K3; RSMD
U$3: ULTRASONIC-HC-SR04#P

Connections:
5V0: U$3.VCC; also elsewhere on the board
GND: R2.1, U$3.GND; also elsewhere on the board
unnamed: R1.1, U$3.ECHO
PE1: U$3.TRIG; also elsewhere on the board
PE2: R1.2, R2.2; also elsewhere on the board

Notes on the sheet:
Powered at 5V. TRIG pin can be 3v3 logic, but ECHO pin needs a shift logic from 5 to 3v3 volt. A simple resistor divider can be used.
Author: Fernando Fontes
HC-SR04. Ultra-Sonic sensor. Common used in distance measuring procedures. In this project, it will be also used to help in the landing, measuring the distance to the ground and also detecting the presence of obstacles.

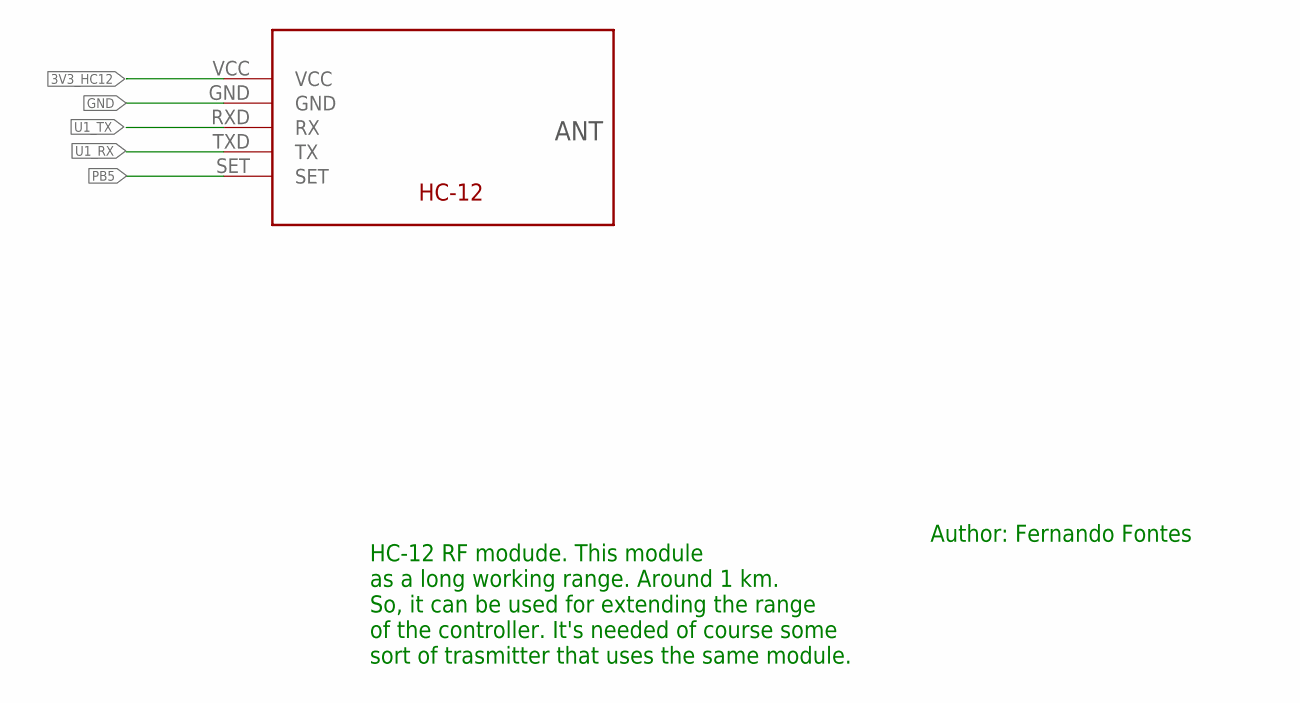
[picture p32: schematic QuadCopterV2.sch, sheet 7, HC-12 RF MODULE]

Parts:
U$5: HC-12_FOOTPRINT

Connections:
3V3_HC12: U$5.VCC; also elsewhere on the board
GND: U$5.GND; also elsewhere on the board
PB5: U$5.SET; also elsewhere on the board
U1_RX: U$5.TXD (TX); also elsewhere on the board
U1_TX: U$5.RXD (RX); also elsewhere on the board

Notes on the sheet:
Author: Fernando Fontes
HC-12 RF modude. This module as a long working range. Around 1 km. So, it can be used for extending the range of the controller. It's needed of course some sort of trasmitter that uses the same module.
ANT

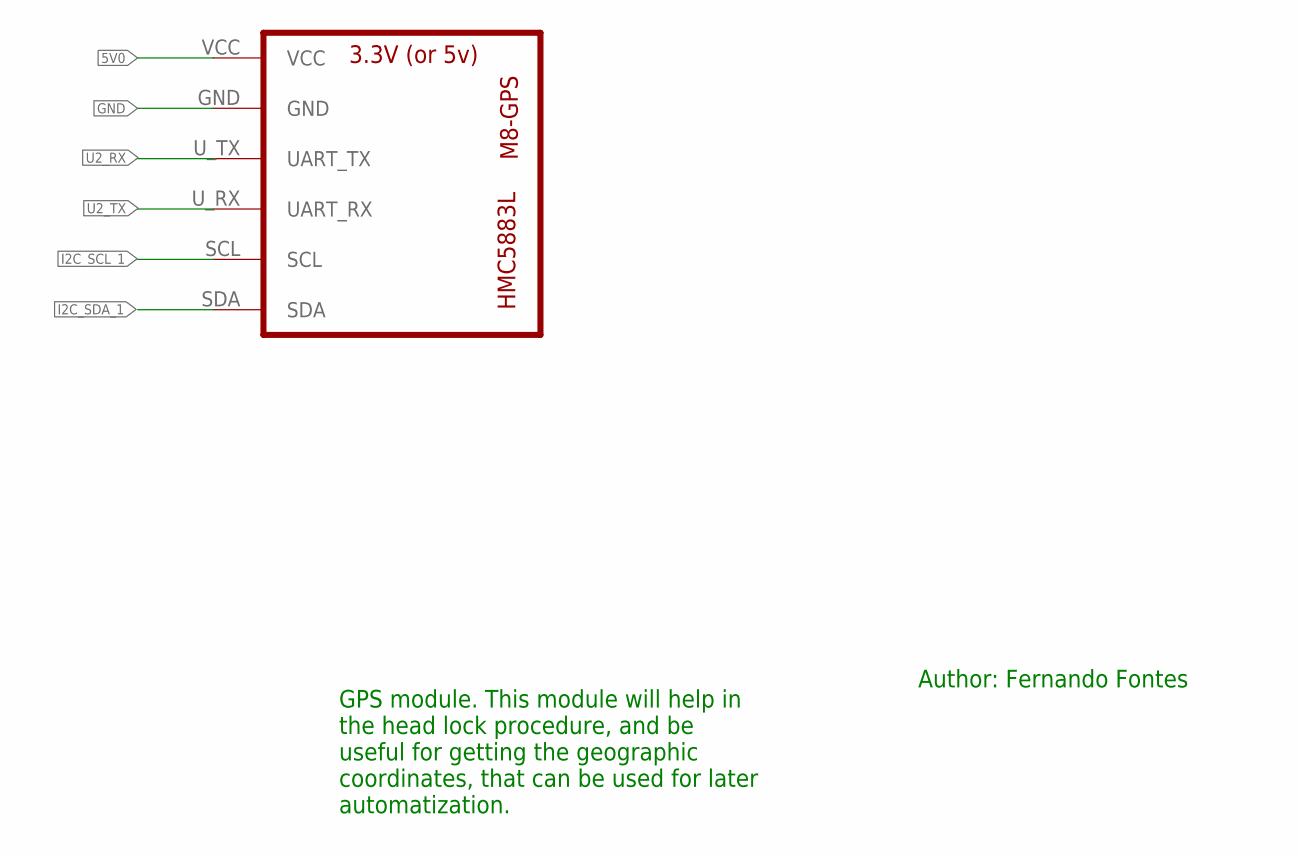
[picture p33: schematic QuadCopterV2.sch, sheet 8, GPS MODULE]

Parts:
U3: GY-63MS5611; U-BLOX

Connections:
5V0: U3.VCC; also elsewhere on the board
GND: U3.GND; also elsewhere on the board
I2C_SCL_1: U3.SCL; also elsewhere on the board
I2C_SDA_1: U3.SDA; also elsewhere on the board
U2_RX: U3.U_TX (UART_TX); also elsewhere on the board
U2_TX: U3.U_RX (UART_RX); also elsewhere on the board

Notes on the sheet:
Author: Fernando Fontes
GPS module. This module will help in the head lock procedure, and be useful for getting the geographic coordinates, that can be used for later automatization.

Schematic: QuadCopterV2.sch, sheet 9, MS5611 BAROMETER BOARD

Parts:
U1: GY-63MS5611; GY-63

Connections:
3V3_MS5611: U1.VCC; also elsewhere on the board
GND: U1.GND; also elsewhere on the board
I2C_SCL_1: U1.SCL; also elsewhere on the board
I2C_SDA_1: U1.SDA; also elsewhere on the board

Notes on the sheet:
Author: Fernando Fontes
Barometer module. This module will be the master piece for the altitude lock mode. Used for locking altitude and to other things.

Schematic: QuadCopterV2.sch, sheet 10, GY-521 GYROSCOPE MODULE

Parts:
U2: GY-521MPU6050; GY-521

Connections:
5V0: U2.VCC; also elsewhere on the board
GND: U2.GND; also elsewhere on the board
I2C_SCL_1: U2.SCL; also elsewhere on the board
I2C_SDA_1: U2.SDA; also elsewhere on the board

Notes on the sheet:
Author: Fernando Fontes
Gyroscope module. Used for the stabilization procedure. Has an internal accelerometer too.
Powered at 5v. However, SCL and SDA lines are 3v3 pulled up. So no need for shift logic converter.

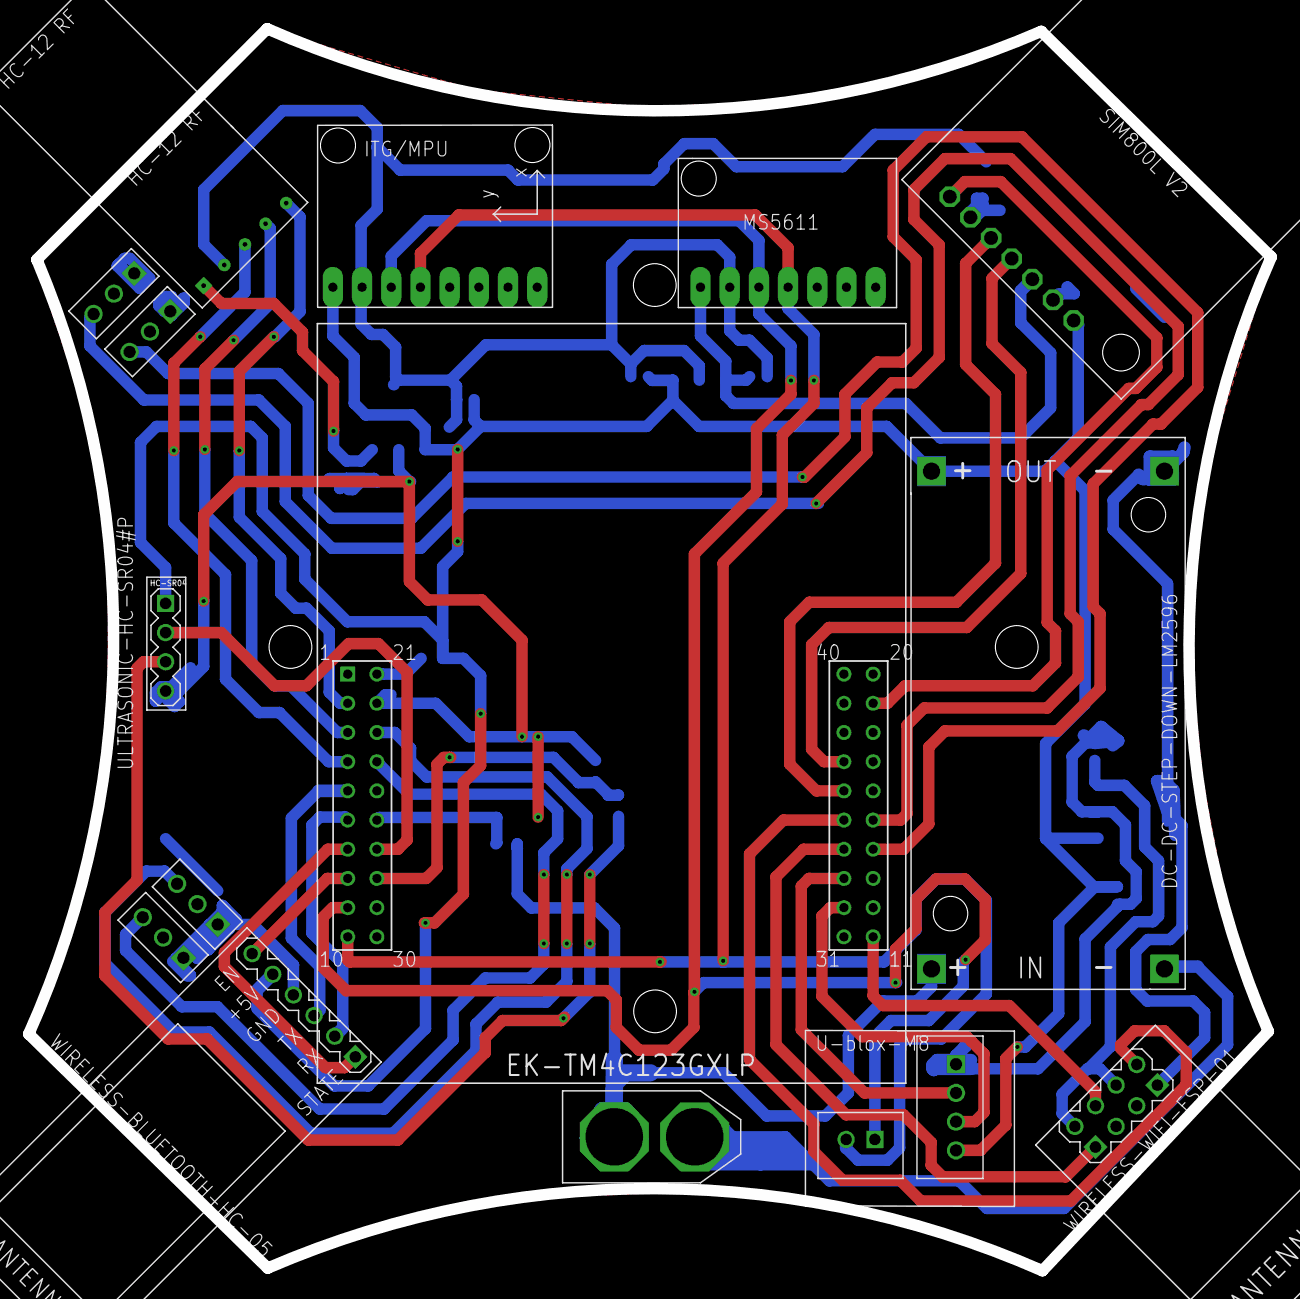
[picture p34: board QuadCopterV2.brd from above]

Board: 2 copper layers, 108.1 x 108.1 mm, 29 parts (0 on the bottom side), 33 nets.

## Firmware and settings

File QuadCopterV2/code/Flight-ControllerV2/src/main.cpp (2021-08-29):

#include <Arduino.h>

#include <interrupt.h>
#include <math.h>
//#include <gpio.h>

#include "hc-05.h"
#include "hc-sr04.h"
#include "HMC5883L.h"
#include "m8-gps.h"
#include "MPU6050.h"
#include "esp-01.h"
#include "hc-12.h"
#include "sim800l.h"
#include "MS5611.h"
#include "quad_pins.h"
#include "util.h"

///////////////// SAFETY DEFINES //////////////
#define QUADCOPTER_MIN_BATTERY_VOLTAGE 9
//////////////////////////////////////////////

///////////////// PID AND OTHERS DEFINES ///////////////
//>>> PID
/* PID General Equation 
 *
 * u(n) = kp  *e(n) + ki  ∑ e(n)T + kd *( e(n)-e(n-1)/T)
 * kp   - proportional gain
 * ki   - integral gain
 * kd   - derivative gain
 * e(n) - setpoint - current value
 * T    - sampling time = 0.004 seconds
 */
//<<< PID EOF

//>>> ALTITUDE
#define QUADCOPTER_MAX_ALTITUDE_ALLOWED 1000 // thrust value
#define QUADCOPTER_ALTITUDE_SCALE_FACTOR (1250.f/QUADCOPTER_MAX_ALTITUDE_ALLOWED)
#define PID_ALTITUDE_MAX_INTEGRAL 50
float PID_ALTITUDE_KP = 0.8f;
float PID_ALTITUDE_KI = 0;
float PID_ALTITUDE_KD = 0;
//<<< ALTITUDE EOF

//>>> ROLL
#define QUADCOPTER_MAX_ROLL_ALLOWED 25  // degrees
#define QUADCOPTER_ROLL_SCALE_FACTOR (625.f/QUADCOPTER_MAX_ROLL_ALLOWED)
#define PID_ROLL_MAX_INTEGRAL 25
float PID_ROLL_KP = 4.8f;
float PID_ROLL_KI = 0.03f;
float PID_ROLL_KD = 0.7;
//<< ROLL EOF

//>>> PITCH
#define QUADCOPTER_MAX_PITCH_ALLOWED 25  // degrees
#define QUADCOPTER_PITCH_SCALE_FACTOR (625.f/QUADCOPTER_MAX_PITCH_ALLOWED)
#define PID_PITCH_MAX_INTEGRAL PID_ROLL_MAX_INTEGRAL
float PID_PITCH_KP  = PID_ROLL_KP;
float PID_PITCH_KI  = PID_ROLL_KI;
float PID_PITCH_KD  = PID_ROLL_KD;
//<< PITCH EOF

//>>> YAW
#define QUADCOPTER_MAX_YAW_ALLOWED 60  // degrees
#define QUADCOPTER_YAW_SCALE_FACTOR (625.f/QUADCOPTER_MAX_YAW_ALLOWED)
#define PID_YAW_MAX_INTEGRAL 25
float PID_YAW_KP = 0; // bug detected 
float PID_YAW_KI = 0;
float PID_YAW_KD = 0;
//<< YAW EOF
////////////////////////////////////////////////////////

////////////////MPU-6050///////////////
MPU6050 accelgyro;
// for angle measurement based on gyro
float gyro_x = 0, gyro_y = 0, gyro_z = 0;
// for angle measurement based on accel
float accel_x = 0, accel_y = 0, accel_z = 0;
float XY_distance, YZ_distance, ZX_distance;
float phi, theta, psi;
// flight variables
float pitch = 0, roll = 0, yaw = 0;
float quad_pitch, quad_roll, quad_yaw;
bool yawFirstTime = true, targetAltitudeFirstTime = true;
//////////////////////////////////////

////////////////HMC5883L///////////////
HMC5883L mag = HMC5883L(0);
// for magnetic measurements 
float magnetic_x, magnetic_y, magnetic_z, heading;
// for tilt correction
float Xh, Yh;
//////////////////////////////////////

////////////////MS5611///////////////
MS5611 baro = MS5611();
// for altitude measurements 
float altitude, temperature, baro_correction_coeff;
//////////////////////////////////////

////////////////GPS///////////////
struct m8_gps gps_coords;
//////////////////////////////////

////////////////SIM800L///////////////
sim800l sim;
//////////////////////////////////

////////////////LOOP///////////////
unsigned long last_loop = 0;
uint32_t count = 0;
uint8_t retval = 0;
char uart0_tx_buffer[100];
char* float_conv_ptr;
char* int_conv_ptr;
uint8_t isNewInc = 0;
unsigned long tic;
unsigned long toc;
bool flag = false;
//////////////////////////////////////

//////////CALIBRATION//////////////
void sw2_isr();
void sw1_isr();
// for magnetometer
bool isMagCal = false;
// for MPU-6050
bool isMpuCal = false;
//////////////////////////////////////

//////////REMOTE////////////
int32_t motor1_thrust = 0;
int32_t motor2_thrust = 0;
int32_t motor3_thrust = 0;
int32_t motor4_thrust = 0;
float target_altitude, thrust_cmd, yaw_cmd, pitch_cmd, roll_cmd, initial_yaw;
float thrust_u, yaw_u, pitch_u, roll_u;
uint16_t ch[4] = { 625, 0, 625, 625 };
uint8_t flags = REMOTE_QUADCOPTER_NO_FLAGS;
////////////////////////////

////////////PID////////////
float thrust_last_error = 0, thrust_error = 0;
float yaw_last_error = 0, yaw_error = 0;
float pitch_last_error = 0, pitch_error = 0;
float roll_last_error = 0, roll_error = 0;
float yaw_integral, roll_integral;
float thrust_integral, pitch_integral;
quad_pid_config * pid_config;
///////////////////////////

void setup() {
    // start initing serial port
    Serial.begin(115200);
    pinMode(PA_4,OUTPUT); // for debugging 
    
    /* --- Init LED's and Analogs --- */
    quad_init();

    /* --- Init ESC Motors --- */
    quad_esc_motors_init();

    /* --- Init rotines to trigger a newer calibration --- */
    pinMode(PF_4,INPUT_PULLUP);
    pinMode(PF_0,INPUT_PULLUP);
    attachInterrupt(PF_4,sw1_isr, FALLING);
    attachInterrupt(PF_0,sw2_isr, FALLING);

    // let voltage stable
    delay(3000);

    // print system information
    quad_redOn();
    Serial.println("System Clock Frequency : " + String(SysCtlClockGet()/1000000) + " Mhz");
    Serial.println("System Battery : " + String(quad_readBatteryVoltage()) + " Volt");
    if(quad_readBatteryVoltage() < QUADCOPTER_MIN_BATTERY_VOLTAGE){
        Serial.println("Not enough power to start ...");
        while(1); // TODO: BLINK
    }

    /* --- Init i2c pins --- */
    Wire = TwoWire(1);
    Wire.begin(); 
    delay(200);

    /* --- Init EEPROM --- */
    Serial.println("Initing EEPROM...");
    if(quad_init_eeprom() == QUAD_OK){
        Serial.println("EEPROM OK!");
        // set magnetometer eeprom callbacks
        mag.setEEPROMWriteFunction(quad_write_eeprom);
        mag.setEEPROMReadFunction(quad_read_eeprom);
        // set mpu6050 eeprom callbacks
        accelgyro.setEEPROMWriteFunction(quad_write_eeprom);
        accelgyro.setEEPROMReadFunction(quad_read_eeprom);
    } else {
        Serial.println("EEPROM NOT OK!");
        while(1); // TODO: BLINK
    }
    // EEPROM Size (bytes) : 2048 EEPROM Bytes Pear Block : 64
    Serial.println("EEPROM Size (bytes) : " + String(quad_eeprom_get_size()) + " EEPROM Bytes Pear Block : " 
                                + String(quad_eeprom_get_bytes_pear_block()));

    /* --- Init HC-05 --- */
    Serial.println("Initing HC-05...");
    if(hc_05_init() == HC_05_OK){
        Serial.println("HC-05 INIT OK ! BAUDRATE = " + String(HC_05_BAUDRATE) + 
        " HC-05 NAME = " + String(HC_05_DEVICE_NAME) + " HC-05 PASS " + String(HC_05_DEVICE_PASS));
        // set state interrupt callback
        HC_05_STATE_INT(hc_05_status_isr);
        // set hc-05 rx interrupt callback
        HC_05_RX_INT(hc_05_rx_isr);
    } else {
        Serial.println("HC-05 INIT FAILED !");
        while(1); // TODO: BLINK
    }
    delay(200);

    /* --- Init HC-12 --- */
    Serial.println("Initing HC-12...");
    if(hc_12_init() == HC_12_OK){
        Serial.println("HC-12 INIT OK ! BAUDRATE = " + String(HC_12_BAUDRATE));
        Serial.println("Channel: " + String(433.4F + hc_12_getRadioChannel()*0.5F ) + "Mhz");
        Serial.print("Device Mode: ");
        switch (hc_12_getDeviceMode()){
        case HC_12_MODERATE_POWER_SAVING_MODE: Serial.println("\"MODERATE POWER SAVING MODE\""); break;
        case HC_12_EXTREME_POWER_SAVING_MODE: Serial.println("\"EXTREME POWER SAVING MODE\""); break;
        case HC_12_GENERAL_PURPOSE_MODE: Serial.println("\"GENERAL PURPOSE MODE\""); break;
        case HC_12_LONG_RANGE_MODE: Serial.println("\"LONG RANGE MODE\""); break;                                
        default: Serial.println("Invalid Mode!"); break; }
        Serial.println("TX Power: " + String(0.8F*pow(2,hc_12_getTXpower()-1)) + "mW");
    } else {
        Serial.println("HC-12 INIT FAILED !");
        while(1); // TODO: BLINK
    }
    delay(200);

    /* --- Init HC-SR04 --- */
    Serial.println("Initing HC-SR04...");
    if(hc_sr04_init(HC_SR04_EXPECTED_HEIGHT) == HC_SR04_0K){
        Serial.println("HC-SR04 INIT OK");
    } else Serial.println("HC-SR04 INIT FAILED");
    delay(200);

    /* --- Init M8_GPS --- */
    Serial.println("Initing M8_GPS...");
    //init M8_GPS
    //// set baudrate
    if(m8_gps_init(M8_GPS_BAUDRATE) == M8_GPS_OK){
        Serial.println("M8_GPS INIT OK ! BAUDRATE = " + String(M8_GPS_BAUDRATE));
        //// change measurement rate
        m8_gps_setMeasRate(M8_GPS_MEASRATE, M8_GPS_NAVRATE);
        //// disable un-necessary messages
        m8_gps_setMsgRate(M8_GPS_RMC_MESSAGE, M8_GPS_MESSAGE_DISABLED);
        m8_gps_setMsgRate(M8_GPS_VTG_MESSAGE, M8_GPS_MESSAGE_DISABLED);
        m8_gps_setMsgRate(M8_GPS_GGA_MESSAGE, M8_GPS_MESSAGE_DISABLED);
        m8_gps_setMsgRate(M8_GPS_GSA_MESSAGE, M8_GPS_MESSAGE_DISABLED);
        m8_gps_setMsgRate(M8_GPS_GSV_MESSAGE, M8_GPS_MESSAGE_DISABLED);
        //// set M8_GPS rx interrupt callback
        M8_GPS_RX_INT(m8_gps_rx_isr);
    } else {
        Serial.println("M8_GPS FAILED!");
        while(1); // TODO: BLINK
    }
    delay(200);

    /* --- Init SIM800L --- */
    Serial.println("Initing SIM800L...");
    sim.shutdown();
    // if(sim.begin(SIM800L_BAUDRATE) == SIM800L_OK){
    //     Serial.println("SIM800L INIT OK ! BAUDRATE = " + String(SIM800L_BAUDRATE));
    //     SIM800L_RX_INT(sim800l_rx_isr);
    // }else {
    //     Serial.println("SIM800L INIT FAILED!");
    //     while(1); // TODO: BLINK
    // }
    // delay(200);

    /* --- Init ESP-01 --- */
    Serial.println("Initing ESP_01...");
    if(esp_01_init() == ESP_01_OK){
        Serial.println("ESP_01 INIT OK ! BAUDRATE = " + String(ESP_01_BAUDRATE));
        /// open tcp connection
        if ( esp_01_tcp_connect((char*)"192.168.100.1",(char*)"9090") == ESP_01_OK ) {
            Serial.println("Listening for connections on port 9090!");
        } else {
            Serial.println("Error while setting TCP port!!!");
        }
        /// set interrupt callback
        ESP_01_RX_INT(esp_01_rx_isr);
    } else {
        Serial.println("ESP_01 INIT FAILED!");
    }
    delay(200);

    /* --- Init HMC5883 --- */
    Serial.println("Initing HMC5883...");
    //init sensor
    if(!mag.begin()) {
        Serial.println("HMC5883 INIT FAILED!");
        while(1); // TODO: BLINK
    } else {
        if(!mag.isCalibrated()) mag.calibrate(30); // calibrate for 30 seconds
        Serial.println("HMC5883 INIT OK!");
    }
    delay(200);

    /* --- MS5611 --- */
    Serial.println("Initing MS5611...");
    if(baro.init(MS5611_ADDR) == MS5611_OK) {
        Serial.println("HMC5883 INIT OK!");
    } else {
        Serial.println("MS5611 INIT FAILED!");
        while(1); // TODO: BLINK
    }
    delay(200);

    /* --- Init MPU6050 --- */
    Serial.println("Initing MPU6050...");
    accelgyro.initialize();
    if(accelgyro.testConnection()){
        // config MPU6050 resolution
        accelgyro.setFullScaleGyroRange(MPU6050_GYRO_FS_500);
        accelgyro.setFullScaleAccelRange(MPU6050_ACCEL_FS_8);
        delay(200);
        if(!accelgyro.isCalibrated()) accelgyro.calibrate(); 
        Serial.println("MPU6050 INIT OK!");
    } else {
        Serial.println("MPU6050 INIT FAILED!");
        while(1); // TODO: BLINK
    }
    delay(200);

    // enable interrupts
    IntMasterEnable();

    // ok :) good to go!
    quad_blueOn();
}

void loop() {
    // elapsed time = 999us - should repeat at every 4 ms
    if((micros() - last_loop) >= MPU6050_READ_PERI) {
        // update last_loop time value
        last_loop = micros();

        if(flag) GPIOPinWrite(0x40004000, 0x10, 0x10);
        else GPIOPinWrite(0x40004000, 0x10, 0x00);
        flag = !flag;

        ///////////MPU6050-READING//////////////////////
        accelgyro.getMotion6(&accel_x, &accel_y, &accel_z, &gyro_x, &gyro_y, &gyro_z);
        ////////////////////////////////////////////////

        ///////////CONVERSIONS//////////////
        // convert accelaration to g-force
        accel_x = accel_x / MPU6050_ACCEL_SCALE_FACTOR;
        accel_y = accel_y / MPU6050_ACCEL_SCALE_FACTOR;
        accel_z = accel_z / MPU6050_ACCEL_SCALE_FACTOR;
        // Convert gyro output to deg
        gyro_x /= MPU6050_GYRO_ANGLE_FACTOR;
        gyro_y /= MPU6050_GYRO_ANGLE_FACTOR;
        gyro_z /= MPU6050_GYRO_ANGLE_FACTOR;
        ////////////////////////////////

        ///////////ANGLES//////////////////////////////////////////////
        // calculates sqrt values
        XY_distance = sqrtf(accel_x*accel_x + accel_y*accel_y);
        YZ_distance = sqrtf(accel_y*accel_y + accel_z*accel_z);
        ZX_distance = sqrtf(accel_z*accel_z + accel_x*accel_x);
        // calculates angles
        theta = atanf(accel_x/YZ_distance) * RAD_TO_DEG;
        psi   = atanf(accel_y/ZX_distance) * RAD_TO_DEG;
        phi   = atanf(XY_distance/accel_z) * RAD_TO_DEG;
        ////////////////////////////////////////////////////////////////

        /////////////////////////REMOVE GYRO DRIFT//////////////////////
        pitch += gyro_x;
        roll += gyro_y;
        yaw += -gyro_z;
        // for tranfering pitch to roll
        pitch += roll * sinf(gyro_z * DEG_TO_RAD);  // pi/180 = 0.01745
        roll -= pitch * sinf(gyro_z * DEG_TO_RAD);     
        // removing drift
        pitch = pitch * 0.9996 + psi * 0.0004;     
        roll = roll * 0.9996 + theta * -0.0004;
        // saturate yaw if needed
        if(yaw > 360) yaw -= 360;
        if(yaw < 0)   yaw += 360; 
        ////////////////////////////////////////////////////////////////

        //////////// TRANSFER MPU6050 COORDS TO QUAD COORDS //////////////
        // mpu6050 can be mounted at different locations on the quadcopter
        // the goal here, is create a calibration program that will assign
        // the mpu6050 coords to the quad coords. Quad coords are based
        // on the GPS Module arrow
        quad_pitch = -roll;
        quad_roll  = pitch;
        //////////////////////////////////////////////////////////////////

        ///////////HMC5883L-READING//////////////////////
        mag.getMotion(&magnetic_x,&magnetic_y,&magnetic_z);
        ////////////////////////////////////////////////

        ///////////CALCULATIONS/////////////////
        /* tilt corrections */
        Xh = magnetic_x*cosf(-quad_pitch*DEG_TO_RAD) + magnetic_y*sinf(quad_roll*DEG_TO_RAD)*sinf(-quad_pitch*DEG_TO_RAD) 
                    - magnetic_z*cosf(quad_roll*DEG_TO_RAD)*sinf(-quad_pitch*DEG_TO_RAD);
        Yh = magnetic_y*cosf(quad_roll*DEG_TO_RAD) + magnetic_z*sinf(quad_roll*DEG_TO_RAD);
        //Now that the horizontal values are known the heading can be calculated. With the following lines of code the heading is calculated in degrees.
        //Please note that the atan2 uses radians in stead of degrees. That is why the 180/3.14 is used.
        if (Yh < 0) heading = 360 + atan2f(Yh, Xh)*RAD_TO_DEG;
        else heading = atan2f(Yh, Xh)*RAD_TO_DEG;  
        ////////////////////////////////////////

        ///////////CORRECTIONS////////////////////
        heading += -1.7667F; // declination correction
        // Correct for when signs are reversed.
        if(heading < 0)   heading += 360;
        // Check for wrap due to addition of declination.
        if(heading > 360) heading -= 360;
        /////////////////////////////////////////

        ////////////////YAW CORRECTIONS//////////////////
        if(yawFirstTime){
            yawFirstTime = false; // not first time anymore
            yaw = heading; // assign heading to yaw
            initial_yaw = yaw - 180;
        }
        // removing yaw drift
        yaw = yaw * 0.9996 + heading * 0.0004; 
        // transfering mpu6050 coords to quad coords
        quad_yaw = yaw;
        /////////////////////////////////////////////

        ///////////  READ ALTITUDE ( < 250 us ) //////////////////
        altitude = baro.iterateSensorAndGetAltitude() / 100.f; // in meters
        temperature = baro.getSensorTemperature() / 100.f; 
        if (targetAltitudeFirstTime) {
            targetAltitudeFirstTime = false; // not first time anymore
            target_altitude = altitude; // assign altitude to target_altitude
        }
        /////////////////////////////////////////////

        //////////// READ REMOTE //////////////////
        if(hc_05_readChannels(ch,&flags) == HC_05_NOT_OK){
            // TODO: READ HC-12
            ch[0] = ch[0]*0.999995 + 625*0.000005;  // In case of losting connection
            ch[1] = ch[1]*0.999995 + 0*0.000005;    // This will increasingly start falling the 
            ch[2] = ch[2]*0.999995 + 625*0.000005;  // quadcopter ...
            ch[3] = ch[3]*0.999995 + 625*0.000005;
        }
        ///////////////////////////////////////////

        /// CONVERT REMOTE TO DEG's AND ALTITUDE //
        yaw_cmd    = ((ch[0]-625)/QUADCOPTER_YAW_SCALE_FACTOR)   ; // -25 ... 0 ... 25 degrees
        thrust_cmd = (ch[1]/QUADCOPTER_ALTITUDE_SCALE_FACTOR)    ; //   0 ... 5 ... 10 thrust
        pitch_cmd  = ((625-ch[3])/QUADCOPTER_PITCH_SCALE_FACTOR) ; // -25 ... 0 ... 25 degrees
        roll_cmd   = ((ch[2]-625)/QUADCOPTER_ROLL_SCALE_FACTOR)  ; // -25 ... 0 ... 25 degrees
        ///////////////////////////////////////////

        /////// IS HOLD ALTITUDE DISABLED ?? ////////
        if ( !(flags & REMOTE_QUADCOPTER_HOLD_ALTITUDE) ) {
            target_altitude = altitude;
        }
        ////////////////////////////////////////////

        /////////// PID CALCULATIONS ///////////////
        // calculate errors
        thrust_error = (target_altitude - altitude);
        pitch_error  = (pitch_cmd  - quad_pitch);
        roll_error   = (roll_cmd   - quad_roll);
        yaw_error    = ((initial_yaw - yaw_cmd) - (quad_yaw-180));

        // calculate and saturate integral
        thrust_integral += thrust_error;
        if(thrust_integral > PID_ALTITUDE_MAX_INTEGRAL) thrust_integral = PID_ALTITUDE_MAX_INTEGRAL;
        if(thrust_integral < -PID_ALTITUDE_MAX_INTEGRAL) thrust_integral = -PID_ALTITUDE_MAX_INTEGRAL;

        pitch_integral += pitch_error;
        if(pitch_integral > PID_PITCH_MAX_INTEGRAL) pitch_integral = PID_PITCH_MAX_INTEGRAL;
        if(pitch_integral < - PID_PITCH_MAX_INTEGRAL) pitch_integral = -PID_PITCH_MAX_INTEGRAL;

        roll_integral += roll_error;
        if(roll_integral > PID_ROLL_MAX_INTEGRAL) roll_integral = PID_ROLL_MAX_INTEGRAL;
        if(roll_integral < -PID_ROLL_MAX_INTEGRAL) roll_integral = -PID_ROLL_MAX_INTEGRAL;

        yaw_integral += yaw_error;
        if(yaw_integral > PID_YAW_MAX_INTEGRAL) yaw_integral = PID_YAW_MAX_INTEGRAL;
        if(yaw_integral < -PID_YAW_MAX_INTEGRAL) yaw_integral = -PID_YAW_MAX_INTEGRAL;

        // calculate control signal
        thrust_u = PID_ALTITUDE_KP * thrust_error + PID_ALTITUDE_KI * thrust_integral + PID_ALTITUDE_KD * (thrust_error - thrust_last_error);
        pitch_u  = PID_PITCH_KP    * pitch_error  + PID_PITCH_KI    * pitch_integral  + PID_PITCH_KD    * (pitch_error  - pitch_last_error);
        roll_u   = PID_ROLL_KP     * roll_error   + PID_ROLL_KI     * roll_integral   + PID_ROLL_KD     * (roll_error   - roll_last_error);
        yaw_u    = PID_YAW_KP      * yaw_error    + PID_YAW_KI      * yaw_integral    + PID_YAW_KD      * (yaw_error    - yaw_last_error);
        
        // update last errors
        thrust_last_error = thrust_error;
        pitch_last_error  = pitch_error;
        roll_last_error   = roll_error;
        yaw_last_error    = yaw_error;
        ///////////////////////////////////////////

        /////// IS HOLD ALTITUDE DISABLED ?? ////////
        if ( !(flags & REMOTE_QUADCOPTER_HOLD_ALTITUDE) ) {
            thrust_u = thrust_cmd;
        } else {
            // slightly compensate for barometer drift
            target_altitude = target_altitude * 0.999998 + altitude * 0.000002;
        }
        ////////////////////////////////////////////

        /////////// CALCULATE MOTOR THRUST ////////
        motor1_thrust = thrust_u + yaw_u - pitch_u - roll_u;
        motor2_thrust = thrust_u - yaw_u - pitch_u + roll_u;
        motor3_thrust = thrust_u - yaw_u + pitch_u - roll_u;
        motor4_thrust = thrust_u + yaw_u + pitch_u + roll_u;
        ///////////////////////////////////////////

        //////////// SET THRUST //////////////////
        motor1_thrust > 0 ? quad_esc_set_thrust(MOTOR1, motor1_thrust) : quad_esc_set_thrust(MOTOR1, 0);
        motor2_thrust > 0 ? quad_esc_set_thrust(MOTOR2, motor2_thrust) : quad_esc_set_thrust(MOTOR2, 0);
        motor3_thrust > 0 ? quad_esc_set_thrust(MOTOR3, motor3_thrust) : quad_esc_set_thrust(MOTOR3, 0);
        motor4_thrust > 0 ? quad_esc_set_thrust(MOTOR4, motor4_thrust) : quad_esc_set_thrust(MOTOR4, 0);
        ///////////////////////////////////////////

        // if isNewInc equals to zero, change back to one and increment 
        if(isNewInc == 0){
            isNewInc = 1;
            count ++;
        }
    }
    
    // have spare time ? play a little bit with it  - max reported - 877us but play safe
    if ( (int) ( MPU6050_READ_PERI - (micros()-last_loop) ) < 1052) return;

    // check if we have new PID params
    if (esp_01_get_pid_params(&pid_config) == ESP_01_OK ) {
        PID_ALTITUDE_KP = pid_config->altitude.p;
        PID_ALTITUDE_KP = pid_config->altitude.i;
        PID_ALTITUDE_KD = pid_config->altitude.d;
        PID_PITCH_KP  = PID_ROLL_KP = pid_config->pitch_and_roll.p;
        PID_PITCH_KI  = PID_ROLL_KI = pid_config->pitch_and_roll.i;
        PID_PITCH_KD  = PID_ROLL_KD = pid_config->pitch_and_roll.d;
        PID_YAW_KP = pid_config->yaw.p;
        PID_YAW_KI = pid_config->yaw.i;
        PID_YAW_KD = pid_config->yaw.d;
    }

    if (isNewInc) {
        // toggle isNewInc - is new increment ? 
        isNewInc = 0;
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

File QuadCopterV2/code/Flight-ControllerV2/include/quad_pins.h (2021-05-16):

#ifndef _QUAD_PINS_H_
#define _QUAD_PINS_H_

#include <pins_energia.h>
#include <stdint.h>
#include <pwm.h>

#define TARGET_SSID "ITHome"
#define TARGET_PWD "pass1234"
#define QUAD_OK 0
#define QUAD_NOT_OK 1

#define MOTOR1  PWM_OUT_6
#define MOTOR2  PWM_OUT_7
#define MOTOR3  PWM_OUT_1
#define MOTOR4  PWM_OUT_0

#define BATTERY_INDICATOR PD_3

// TODO: ADD here all the necessary functionalities
#define REMOTE_QUADCOPTER_NO_FLAGS       0
#define REMOTE_QUADCOPTER_HOLD_ALTITUDE  (1 << 0)
#define REMOTE_QUADCOPTER_AUTOMATIC_LAND (1 << 1)
#define REMOTE_QUADCOPTER_GPS_HOLD       (1 << 2)

void quad_init();
float quad_readBatteryVoltage();
void quad_redOn();
void quad_greenOn();
void quad_blueOn();
void quad_ledOff();
void quad_led(uint8_t led, uint8_t state);
void quad_blinkLed(uint32_t blink_rate, uint32_t blink_ms, uint8_t led);
void quad_setColor(uint8_t red, uint8_t green, uint8_t blue);

uint8_t quad_write_eeprom(uint32_t addr, uint32_t * data, uint32_t len);
uint8_t quad_read_eeprom(uint32_t addr, uint32_t * data, uint32_t len);
uint32_t quad_eeprom_get_size();
uint8_t quad_eeprom_get_bytes_pear_block();
uint8_t quad_init_eeprom();

void quad_esc_motors_init();
void quad_esc_set_thrust(uint32_t motor, uint16_t throttle);

#endif

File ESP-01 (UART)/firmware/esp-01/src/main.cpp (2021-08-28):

#include <ESP8266WiFi.h>
#include <ESP8266mDNS.h>
#include <WiFiUdp.h>
#include <ArduinoOTA.h>

#define NUMBER_OF_KNOWN_SSIDs 3
#define MAX_STRING_SIZE 20

char ssid[NUMBER_OF_KNOWN_SSIDs][MAX_STRING_SIZE] ={ 
    "ITHome\0",
    "HUAWEI-E5776-D797\0",
    "WiFi-Tixa\0"
};

char password[NUMBER_OF_KNOWN_SSIDs][MAX_STRING_SIZE] = {   
    "pass1234\0",
    "MFQ548R8\0",
    "atixacheiramal\0"
};

char* host = (char*)"000.000.000.000\0";
uint16_t port = 0;

unsigned long last_time = 0;
char _uart_rx_buffer[500] = {'\0'};
char _uart_tx_buffer[500] = {'\0'};
uint16_t _uart_rx_buffer_len = 0;
uint16_t _uart_tx_buffer_len = 0;

// Use WiFiClient class to create TCP connections
WiFiClient client;
bool isConnectedTCPServer = false;
bool isToConnectTCPServer = false;
bool ota_initialized = false;

void connect_to_wifi() {
    // setup variables
    uint8_t i=0, j=0, n=0;
    bool isKnown = false;
    // change wifi mode to wifi sta and disconnect from possible connected network
    WiFi.mode(WIFI_STA);
    WiFi.disconnect();
    // enter in discovery mode and list access points
    // search a known network
    //Serial.println("Scanning Networks ...");
    n = WiFi.scanNetworks();
    // go through all scanned ssids and check if we have the authentication parameters
    for (i = 0; i < n; i++) {
        //Serial.println(WiFi.SSID(i));
        for(j = 0; j < NUMBER_OF_KNOWN_SSIDs; j++){
            // compare ssid with known ssids
            if(strcmp(ssid[j],WiFi.SSID(i).c_str()) == 0){
                isKnown = true;
                break;
            }
        }
        if (isKnown) {
            break;
        }
    }

    if (isKnown) {
        // try to connect if isknown
        // Serial.printf("Trying to connect to SSID[%d]: %s",j,ssid[j]);
        WiFi.begin(ssid[j], password[j]);
        if (WiFi.waitForConnectResult() != WL_CONNECTED) {
            // Serial.println("Connection failed! Rebooting...");
            WiFi.disconnect();
        }
    }
}

void configure_ota() {
    // configurations for OTA

    // change ota port
    ArduinoOTA.setPort(8266);

    // change esp hostname
    ArduinoOTA.setHostname("ESP8266-JF");

    // set password
    // ArduinoOTA.setPassword((const char *)"123");

    // set ota callbacks
    ArduinoOTA.onStart([]() {
        Serial.printf("OTA onStart()...\r");
    });

    ArduinoOTA.onEnd([]() {
        Serial.printf("OTA onEnd()...\r");
    });

    ArduinoOTA.onProgress([](unsigned int progress, unsigned int total) {
        Serial.printf("\rOTA onProgress(): %u%%", (progress / (total / 100)));
    });

    ArduinoOTA.onError([](ota_error_t error) {
        Serial.printf("OTA onError() [%u]: \r", error);
        if (error == OTA_AUTH_ERROR) Serial.printf("Authentication Failed\r");
        else if (error == OTA_BEGIN_ERROR) Serial.printf("Begin error\r");
        else if (error == OTA_CONNECT_ERROR) Serial.printf("Connection Failed\r");
        else if (error == OTA_RECEIVE_ERROR) Serial.printf("Error while receiving\r");
        else if (error == OTA_END_ERROR) Serial.printf("End failure\r");
    });

    // start ota
    ArduinoOTA.begin();

    ota_initialized = true;
}

void setup() {
    // start by initing serial port for debug 
    Serial.begin(115200);
    Serial.printf(">OK\r");

    // Ok ! done, print IP
    //Serial.print("OK, IP: ");
    //Serial.println(WiFi.localIP());

    // go to loop();
    last_time = millis();
}

void loop() {
    if (ota_initialized && (WiFi.status() == WL_CONNECTED)) {
        // check possible updates
        ArduinoOTA.handle();
    } else if (WiFi.status() == WL_CONNECTED) {
        configure_ota();
    }

    // read commands from uart rx
    if(Serial.available()){
        _uart_rx_buffer_len += Serial.readBytesUntil('\r',&_uart_rx_buffer[_uart_rx_buffer_len],sizeof(_uart_rx_buffer)-_uart_rx_buffer_len);
        _uart_rx_buffer[_uart_rx_buffer_len] = '\0';

        // check if is a inner command
        if(String(_uart_rx_buffer).indexOf('#') != -1){
            
            //// #TCP,IP,PORT
            if(String(_uart_rx_buffer).indexOf("#TCP,") != -1){
                //// init ip and port variables
                String ip = "";
                String po = "";
                //// try set ip and port
                ip = String(_uart_rx_buffer).substring(5);
                po = ip.substring(ip.indexOf(',')+1,ip.length());
                ip = ip.substring(0,ip.indexOf(','));
                //// validate ip and port
                if((ip != "") && (po != "")){
                    //// try cpy ip to host
                    strcpy(host,ip.c_str());
                    //// try convert port o int
                    port = po.toInt();
                    if(port != 0){
                        Serial.printf(">OK\r");
                        isToConnectTCPServer = true;
                    }
                    else Serial.printf(">ERROR\r");
                } else Serial.printf(">ERROR\r");
            }

            //// #TPCCLOSE
            else if(String(_uart_rx_buffer).indexOf("#TPCCLOSE") != -1){
                isToConnectTCPServer = false;
                Serial.printf(">OK\r");
            }
            
            //// just confirm that you are alive
            else{
                Serial.printf(">OK\r");
            }

            //// clean buffer
            memset(_uart_rx_buffer,'\0',_uart_rx_buffer_len);
            //// reset length
            _uart_rx_buffer_len = 0;
        }  
    }

    if (isToConnectTCPServer && (WiFi.status() != WL_CONNECTED)) {
        connect_to_wifi();
    }

    // try connecting to a tcp server every 5 seconds if isToConnectTCPServer
    if(((millis()-last_time) >= 5000) && (WiFi.status() == WL_CONNECTED) && (!isConnectedTCPServer) && (isToConnectTCPServer) ){
        // update last time
        last_time = millis();

        // check connection status
        if (client.connect(host, port)){

            // flag isConnectedTCPServer
            isConnectedTCPServer = true;

            // send hello to the server
            client.printf("Hello from Quadcopter V2\n");

            // send connected via tx
            Serial.printf(">CONNECTED\r");
        }
    }

    // if connected to tcp server check if new messages and print older ones
    if(isConnectedTCPServer && isToConnectTCPServer && (client.status() != CLOSED)){

        //// check if have characters to send 
        if(_uart_rx_buffer_len > 0){
            //// send it
            client.print(_uart_rx_buffer);
            //// clean buffer
            memset(_uart_rx_buffer,'\0',_uart_rx_buffer_len);
            //// update _uart_rx_buffer
            _uart_rx_buffer_len = 0;
        }
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

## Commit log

2020-02-27 first push, with hardware datasheets
    [QuadCopterV2.brd, QuadCopterV2.sch]
2020-03-08 Eagle board design in process
    [QuadCopterV2.brd, QuadCopterV2.sch]
2020-03-17 added modifications to eagle board, and to the mpu-6050 code
    [MPU6050_analysis.xlsx, QuadCopterV2.brd, QuadCopterV2.sch]
2020-03-18 mpu-6050 finished, added more board eagle files, added altimeter code
    [MPU6050_analysis.xlsx, QuadCopterV2.brd, QuadCopterV2.sch]
2020-03-19 Added ESC modules
2020-03-20 news modifications on designed board
    [QuadCopterV2.brd, QuadCopterV2.sch]
2020-03-21 final version of quadcopter board
    [QuadCopterV2.brd, QuadCopterV2.sch]
2020-03-23 added board rendered version
    [QuadCopterV2.brd, QuadCopterV2.sch]
2020-06-18 board sended to production
    [QuadCopterV2.brd]
2020-06-18 added board render
2020-07-22 pcb arrived, some modules already soldered and tested
2020-07-26 added eeprom saving calibration support
2021-03-06 Added PID controllers. Tested and working! KPI needs to be adjusted.
2021-03-07 Added Python-GUI for helping the PID adjusting process. Fixed HC-05 issues
    [quadcopter_raw.csv]
2021-03-14 updates to pid controller
    [quadcopter_raw.csv]
2021-05-16 fixed inaccurate readings from the barometer sensor. Removed altitude PID, since we can't assure an accurate altitude reading and added hold altitude instead.
    [MS5611.cpp, MS5611.h, hc-05.cpp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]
2021-08-28 added tool for setting the PID params remotly
    [quadcopter_raw.csv]
2021-08-29 final touch to the pid setter script
    [quadcopter_raw.csv]

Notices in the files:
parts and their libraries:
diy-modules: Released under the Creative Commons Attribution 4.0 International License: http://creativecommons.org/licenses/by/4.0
